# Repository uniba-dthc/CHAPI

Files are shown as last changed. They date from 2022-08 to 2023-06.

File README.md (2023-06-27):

 
# CHAPI

Meet CHAPI (Cultural Heritage Automated Photogrammetric Imager), a low cost solution which provides a method for capturing large ceiling paintings in high detail, with a consistent photogrammetric network in limited time.

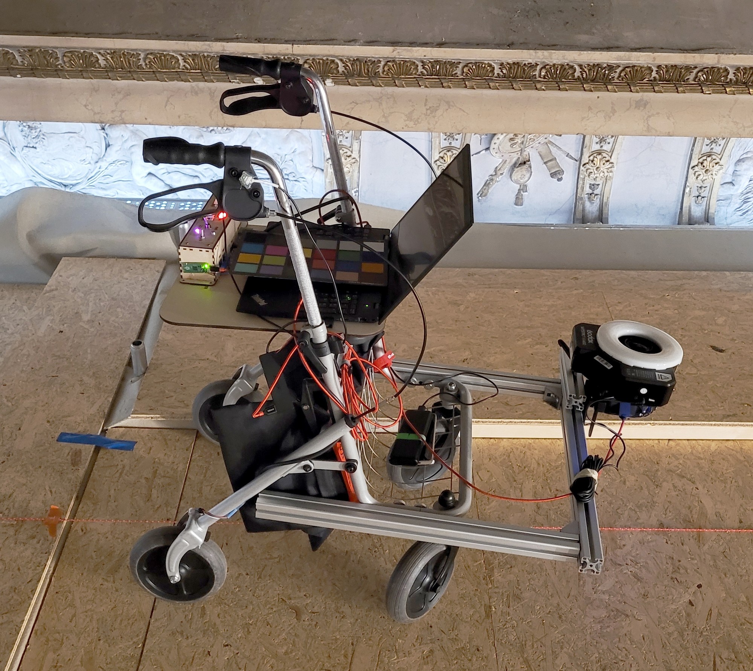
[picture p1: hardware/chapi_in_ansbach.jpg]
CHAPI in Ansbach


# Goals

-  a stable, mobile platform on which a camera could be mounted in multiple orientations
-  a method of automatically measuring distance with a resolution sufficient for a dense photogrammetric network
-  a method of automatically triggering a camera tethered to a laptop
-  a low-cost solution that was also easy to assemble/disassemble for transport.

# Field Assembly

CHAPI is constructed to be assembled and dissembled for ease of transportation. 
As of now the only tool needed is a singe allen key, with the goal of converting all joints to tool less fasteners in the future.

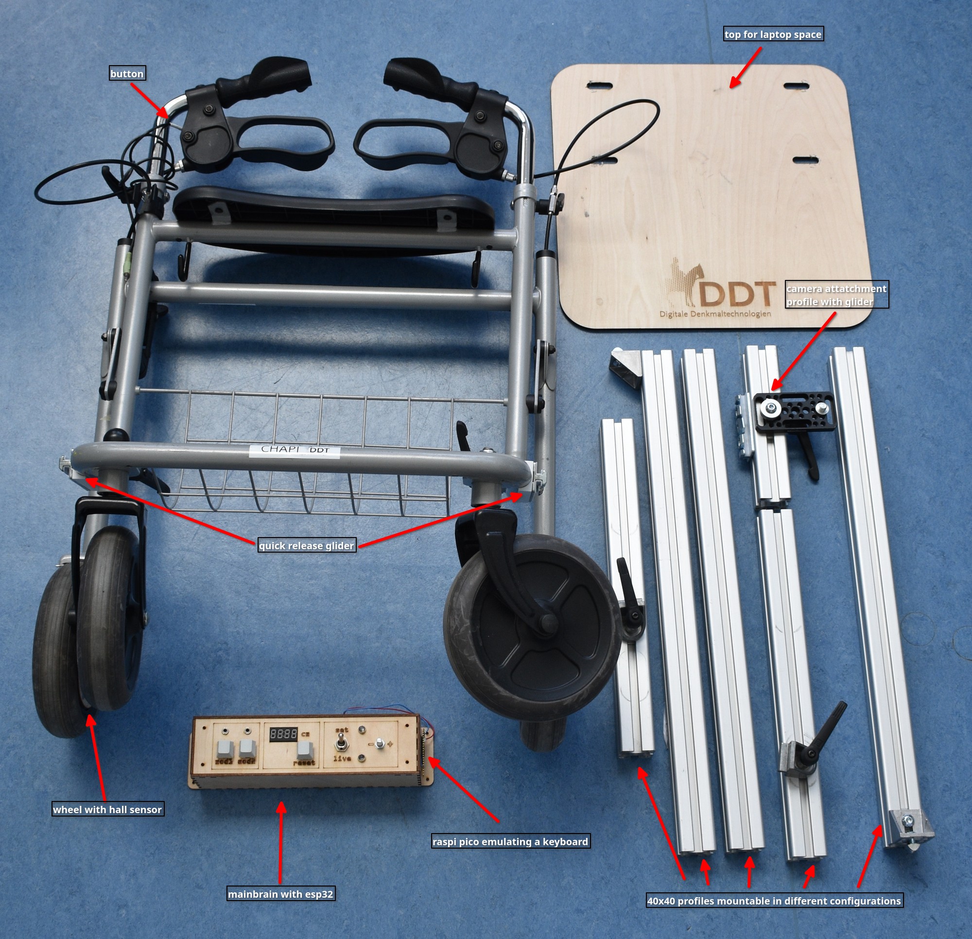
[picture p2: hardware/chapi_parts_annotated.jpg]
CHAPI Parts


1. Fold up the walking frame and extend the handles to a comfortable height.
2. Attach the wooden top plate to the walking frame.
3. Attach the construction profiles to the frame by sliding them onto the gliders.
4. Build with the other construction profiles to the desired height and angle.
5. Connecting the main brain to all the sensors and laptop is just plug and play.
	1. Connect the hall sensor next to the wheel.
	2. Connect the button on the handle.
	3. Connect the laptop to the Raspberry Pi Pico on the side of the main brain.
	4. Connect the main brain ESP32 to a power source, such as a power bank.
6. Add the camera and connect it to the laptop.

Happy imaging!

# License

The project is licensed under MIT License to encourage the community to improve and adapt to their own needs and use cases. 
We hope that modifications and improvements will be made available under the same terms.

# ACKNOWLEDGEMENTS

CHAPI was created by Michael Groh for the [Department of Digital Technologies in Heritage Conservation](https://www.uni-bamberg.de/en/iadk/heritage-conservation-studies/digital-technologies-in-heritage-conservation/), part of the [Centre for Heritage Conservation Studies and Technologies (KDWT)](https://www.uni-bamberg.de/en/iadk/heritage-conservation-studies/centre-for-heritage-conservation-studies-and-technologies-kdwt/) at [University of Bamberg](https://www.uni-bamberg.de/en/). Special thanks to John Hindmarch for his expertise, valuable insights, and testing.

# Publication

Hindmarch, J., Hess, M., Groh, M., & Burioni, M. (2023). A SEMI-AUTOMATED METHODOLOGY FOR 3D IMAGING OF LARGE VAULTED CEILING PAINTINGS. _The International Archives of the Photogrammetry, Remote Sensing and Spatial Information Sciences_, _XLVIII-M-2–2023_, 721–727. https://doi.org/10.5194/isprs-archives-XLVIII-M-2-2023-721-2023

# Availability

- [University of Bamberg Gitlab](https://gitlab.rz.uni-bamberg.de/ddt-public/chapi)
- [Github](https://github.com/uniba-dthc/CHAPI)

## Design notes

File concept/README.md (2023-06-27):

CHAPI incorporates different concepts previously explored on different locations we did surveys. 

# Weikersheim and Dresden

While the features of Weikersheim and Dresden were completely different, one being a well persevered and the other being a bombed out in the second world war, the setup was nearly identical.
We had over 8m clearance to the ceiling and had a completely empty room.
We secured a tripod on a small portable golf cart and attached three (Weikersheim) or four (Dresden) cameras on a bar.

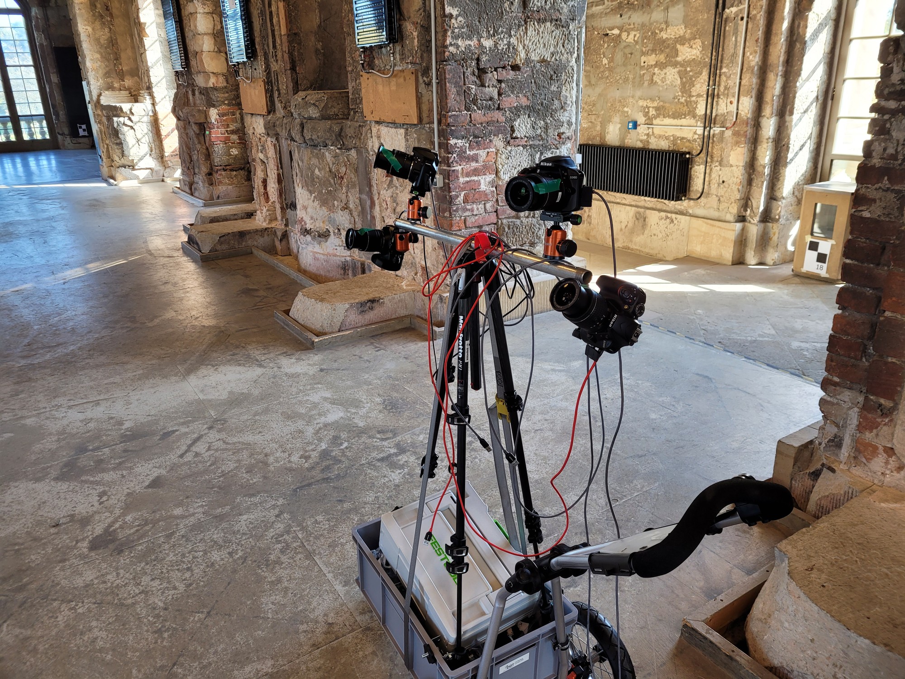
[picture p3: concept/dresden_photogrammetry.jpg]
Golf cart with four cameras


# Ansbach

In Ansbach the 250m² ceiling is undergoing major restoration work and thus a scaffolding platform covers the entire area of the hall, with an approximate 2m clearance to the ceiling. 
The scaffolding enabled the imaging of the fresco in high resolution from close range, but also provided us with the challenge of camera placement within limited space.
Our first step of taking on that challenge was to tape a camera to a rolling board we had at hand for moving our equipment around. 
Also we conducted a test with a tripod on its smallest extension for capturing the wall parts of the fresco.
Both setups were operated by two persons, one moving the board around in a planed out grid, the other one operating a laptop for validating the image quality and giving instructions to the board person.

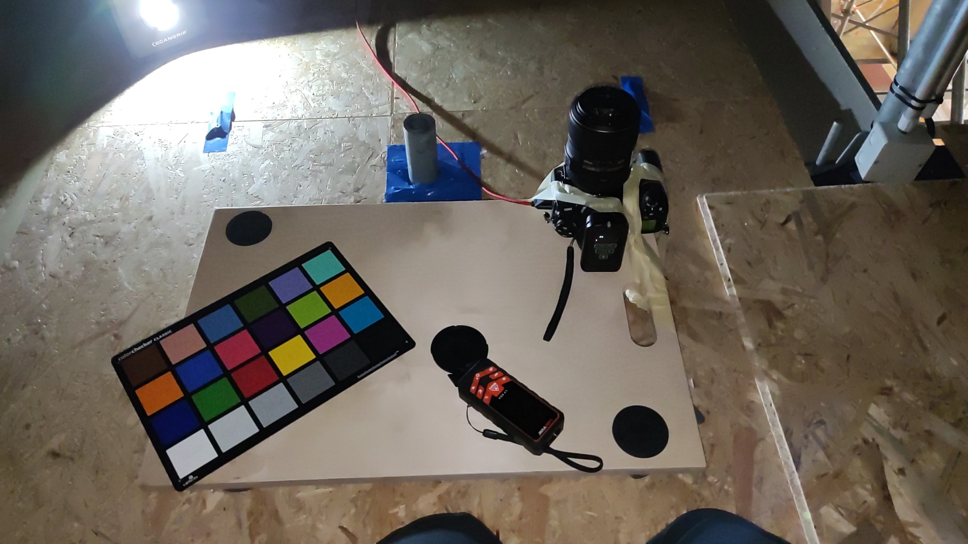
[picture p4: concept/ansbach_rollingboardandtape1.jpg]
Rolling board with a camera taped to it

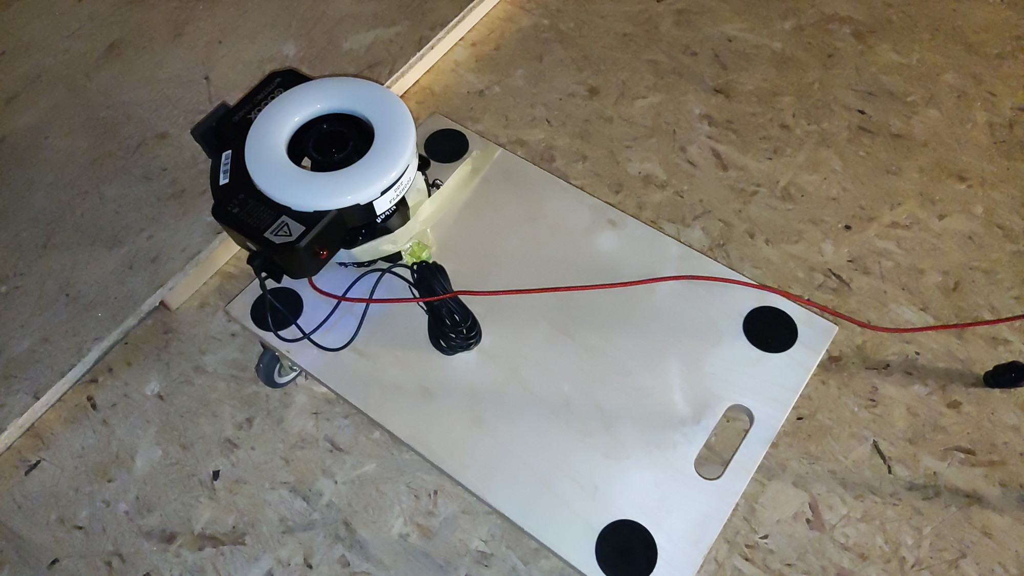
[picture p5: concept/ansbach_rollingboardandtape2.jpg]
Rolling board with a camera and ring flash taped to it

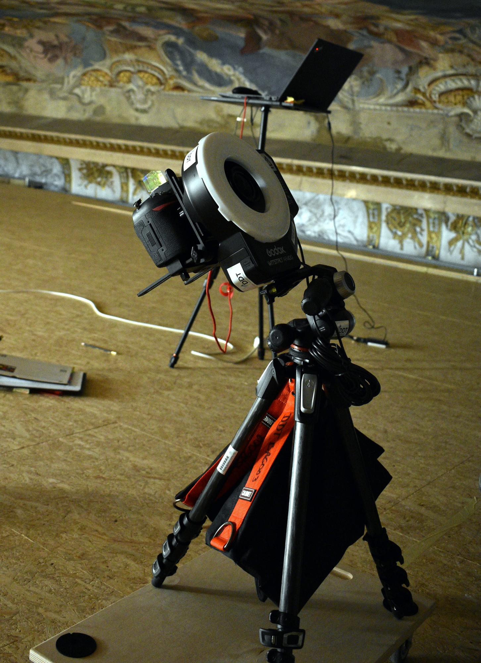
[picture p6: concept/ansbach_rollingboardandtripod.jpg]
Rolling board with a tripod taped to it carrying the ring flash with camera


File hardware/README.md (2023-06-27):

# Parts

* Walking Frame 
	* MEYRA Ideal Rollator, Silber 
	* Product number: 3061982
	* Weight: ca 9 kg
	* Max. load: 130 kg
	* PU-tires
	* [MEYRA Manuals](http://kisss-by-meyra.de/ALLdokuarchiv.php?suche=Ideal%20Rollator)
	* [MEYRA Produkt Page](https://www.meyra.de/reha-pflege-alltagshilfen/reha-und-alltag/reha-alltag-details/product-313/)
* ESPdevboard
* Raspberry Pi Pico
	* [Documentation](https://www.raspberrypi.com/documentation/microcontrollers/raspberry-pi-pico.html)
* Other Electronics Parts
	* Modules
		* TM1637 4 Digit 7-Segment Display  
		* Rotary Encoder
		* Linear Magnetic Hall Sensor
	* Kailh BOX Jade Switches
	* Audio Jack 3.5mm
	* LEDs
	* JST-SM 2.54 2pin terminal connector wire cable
* Construction Profiles
	* 40x40 Type I from [Dold Mechatronik](https://www.dold-mechatronik.de/Aluminum-profile-40x40L-I-type-groove-8)
* Printed parts
	* created with [openscad](https://openscad.org/)
* Lasercut parts
	* boxes generated with [boxes.py](https://www.festi.info/boxes.py/)
* Lots of hot glue

# Details

## Wheel

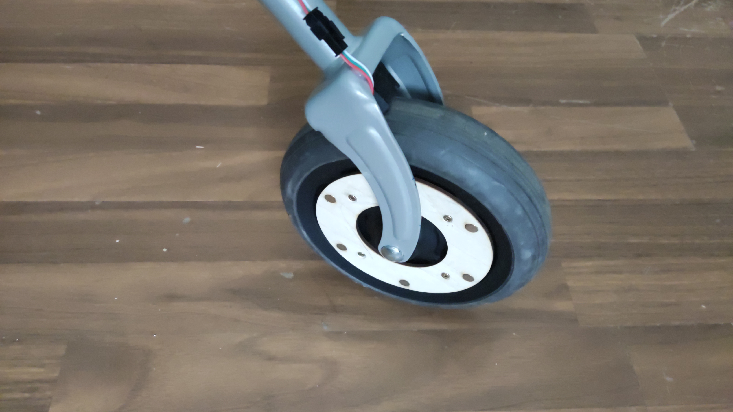
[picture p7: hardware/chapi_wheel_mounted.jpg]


## Mainbrain

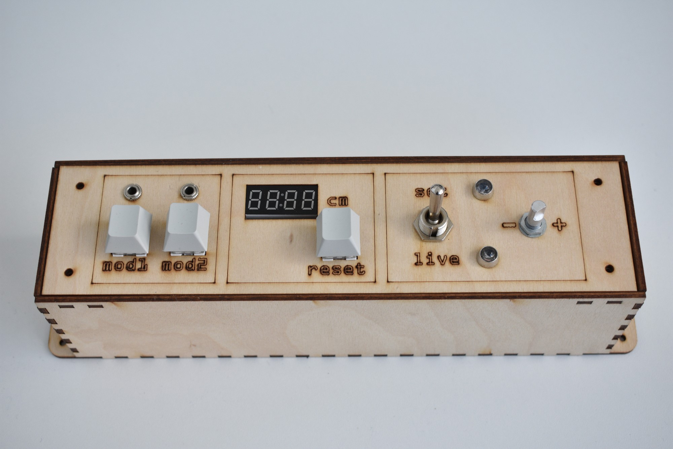
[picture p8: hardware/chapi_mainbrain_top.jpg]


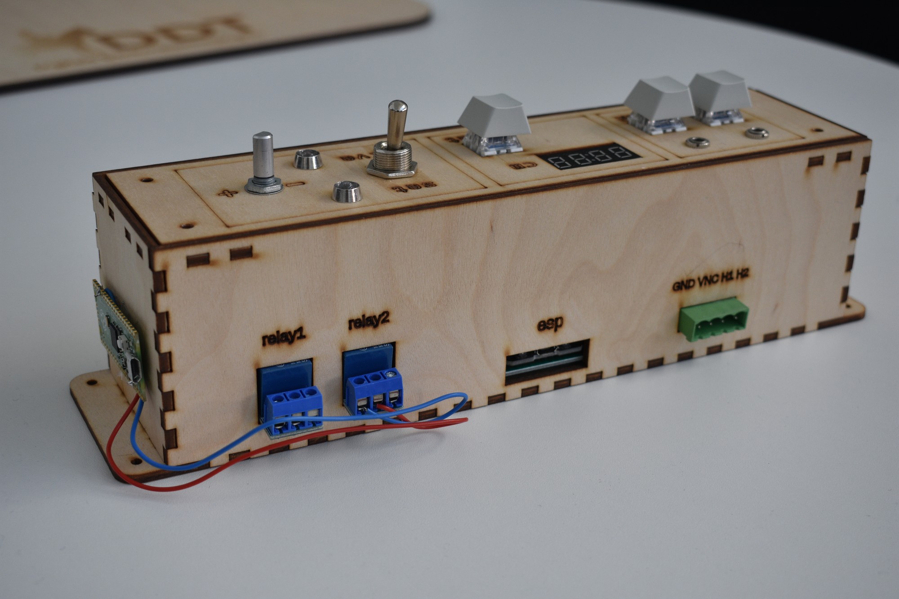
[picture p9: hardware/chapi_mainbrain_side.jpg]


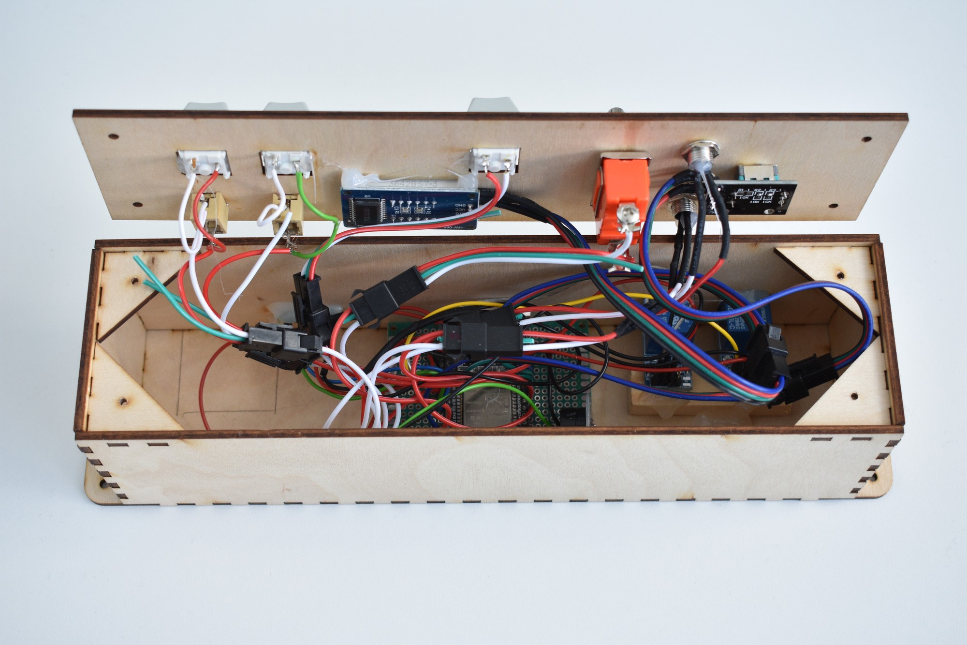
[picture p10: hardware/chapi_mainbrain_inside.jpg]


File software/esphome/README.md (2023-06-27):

# Setup esp home

1. install esp home https://esphome.io/guides/installing_esphome.html https://stackoverflow.com/a/59436732
2. `esphome dashboard config/`
3. dashboard ip will be promted

The main units logic is [chapi-mainbrain.yaml](esphome/config/chapi-mainbrain.yaml). There is more hardware build in, to adjust tho the current use case.

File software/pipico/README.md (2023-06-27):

# Pi setup 

- [Installing CircuitPython](https://learn.adafruit.com/getting-started-with-raspberry-pi-pico-circuitpython/circuitpython)
- The Pi Pico mimics a Keyboard to interact with a PC. It uses the [Adafruit HID Library](https://docs.circuitpython.org/projects/hid/en/latest/index.html)
- [code.py](pipico/code.py) is a modified version of the [code snipped](https://gist.github.com/idriszmy/637a422f1f34a5ee9d2d1f3f614cd7db) form [the tutorial from Idris Zainal Abidin](https://www.cytron.io/tutorial/keyboard-emulator-using-raspberry-pi-pico-maker-pi-pico-and-circuitpython)

# Pinout

Pinout

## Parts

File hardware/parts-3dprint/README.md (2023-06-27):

3D parts were designed with [OpenSCAD](https://openscad.org/).

# Glider support

This support provides more stability to the quick release gilder on both sides of CHAPI.





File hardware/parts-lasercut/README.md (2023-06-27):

Parts for laser cutting were either  created with inkscape or in case of boxes created with [poxes.py ](https://www.festi.info/boxes.py/) and afterwords modified with incscape to add more features.
For some parts there are previous versions and experimental files available. Final versions of a part have the `_path` at the end of the filename.

# Mainbrain





# Wheel



# Top



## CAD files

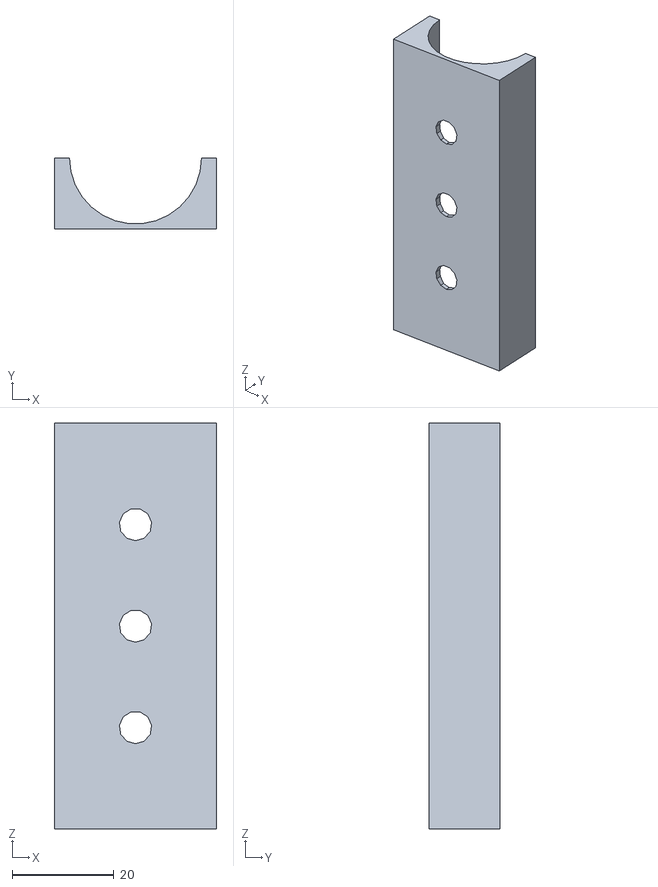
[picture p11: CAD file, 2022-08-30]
hardware/parts-3dprint/pipebracket.stl
32.0 x 14.0 x 80.0

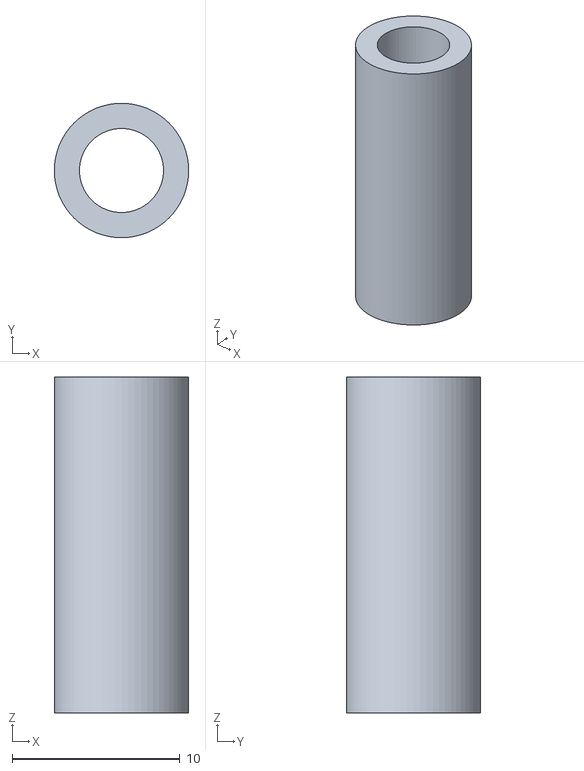
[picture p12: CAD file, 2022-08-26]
hardware/parts-3dprint/pipeinserts.stl
8.00 x 8.00 x 20.0

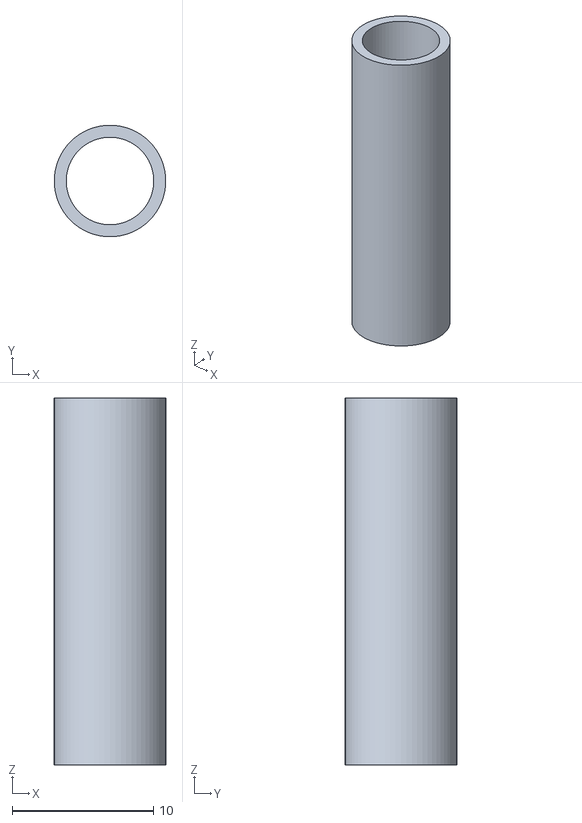
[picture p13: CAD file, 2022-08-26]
hardware/parts-3dprint/pipeinserts8-6.stl
7.90 x 7.90 x 26.0

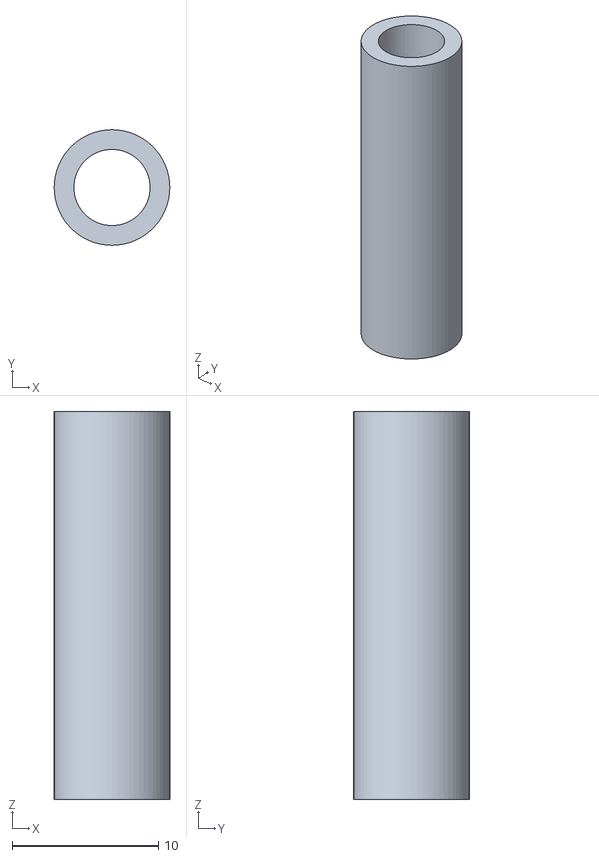
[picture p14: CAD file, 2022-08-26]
hardware/parts-3dprint/pipeinserts8-5.stl
7.90 x 7.90 x 26.5

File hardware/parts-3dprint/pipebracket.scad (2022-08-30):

pipediameter=26;
minthickness=1;
holediameter=6.4;
cubey=pipediameter+minthickness+minthickness;

difference(){
    cube([32,cubey,80],center = true);
    cylinder(h=82,d=pipediameter,center = true);
    group(){ 
        translate([0,0,0])  rotate([0,90,90]) cylinder(h=40,d=holediameter,center = true);
        translate([0,0,20]) rotate([0,90,90]) cylinder(h=40,d=holediameter,center = true);
        translate([0,0,-20])rotate([0,90,90]) cylinder(h=40,d=holediameter,center = true);
    }
    translate([0,(cubey+.1)/2,0])cube([32.1,cubey+.1,80.1],center = true);
}
    

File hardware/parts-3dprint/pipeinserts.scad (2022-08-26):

$fn=64;


difference(){
    cylinder(h=26, d=8-0.1,center= true);
    cylinder(h=30, d=6+0.2,center= true);
    
}

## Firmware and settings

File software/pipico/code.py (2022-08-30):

#
# Keyboard Emulator Using Maker Pi Pico and CircuitPython
#
# References and credit to
# - https://learn.adafruit.com/circuitpython-essentials/circuitpython-hid-keyboard-and-mouse
#
# Raspberry Pi Pico
# - [Maker Pi Pico] https://my.cytron.io/p-maker-pi-pico?tracking=idris
#
# Additional Libraries
# - adafruit_hid
#
# Update:
# 12 Feb 2021 - Tested with CircuitPython Pico 6.2.0-beta.2
#

import time

import board
import digitalio
import usb_hid
from adafruit_hid.keyboard import Keyboard
from adafruit_hid.keyboard_layout_us import KeyboardLayoutUS
from adafruit_hid.keycode import Keycode

# A simple neat keyboard demo in CircuitPython

# The pins we'll use, each will have an internal pullup
keypress_pins = [board.GP13]
# Our array of key objects
key_pin_array = []
# The Keycode sent for each button, will be paired with a control key
keys_pressed = [Keycode.K]
control_key = Keycode.LEFT_CONTROL

# The keyboard object!
time.sleep(1)  # Sleep for a bit to avoid a race condition on some systems
keyboard = Keyboard(usb_hid.devices)
keyboard_layout = KeyboardLayoutUS(keyboard)  # We're in the US :)

# Make all pin objects inputs with pullups
for pin in keypress_pins:
    key_pin = digitalio.DigitalInOut(pin)
    key_pin.direction = digitalio.Direction.INPUT
    key_pin.pull = digitalio.Pull.DOWN
    key_pin_array.append(key_pin)

# For most CircuitPython boards:
led = digitalio.DigitalInOut(board.LED)
led.direction = digitalio.Direction.OUTPUT

print("Waiting for key pin...")

while True:
    # Check each pin
    for key_pin in key_pin_array:
        if not key_pin.value:  # Is it grounded?
            i = key_pin_array.index(key_pin)
            print("Pin #{} is grounded.".format(i))

            # Turn on the red LED
            led.value = True

            while not key_pin.value:
                pass  # Wait for it to be ungrounded!
            # "Type" the Keycode or string
            key = keys_pressed[i]  # Get the corresponding Keycode or string
            if isinstance(key, str):  # If it's a string...
                keyboard_layout.write(key)  # ...Print the string
            else:  # If it's not a string...
                keyboard.press(control_key, key)  # "Press"...
                keyboard.release_all()  # ..."Release"!

            # Turn off the red LED
            led.value = False

    time.sleep(0.01)

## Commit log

2022-08-26 first setup ansbach
    [lochhuelsen.scad, lochhuelsen.stl, lochhuelsen8-5.stl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]
2022-08-26 rohraufleger hinzugefügt
    [rohraufleger.scad, rohraufleger.stl]
2022-08-30 bigger holes
    [rohraufleger.scad, rohraufleger.stl]
2023-06-27 better structure
    [pipebracket.scad, pipebracket.stl, pipeinserts.scad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]
